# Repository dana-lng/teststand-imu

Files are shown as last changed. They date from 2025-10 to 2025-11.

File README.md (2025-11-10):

# Two-Axis IMU Calibration Test Stand with Differential Gear System
An open-source, dual-axis calibration platform for IMU sensors (e.g., MPU6050), featuring a fully 3D-printed differential gear drive and automated motion control for precise in-situ calibration.

## Project Overview

This project presents the design and function of a **two-axis IMU calibration test stand**, developed to calibrate inertial measurement units (IMUs) such as the [MPU6050](https://invensense.tdk.com/products/motion-tracking/6-axis/mpu-6050/). The test stand enables controlled, repeatable motion for precise sensor calibration.

All mechanical parts are **3D printed**, and motion is driven by **NEMA 17 stepper motors** in combination with an **HTD belt system**. The movement is realized through a **differential gear mechanism**, providing two degrees of freedom (DoF).

The Calibration is based on the method proposed in the following paper:
> **A. Mikov, S. Reginya, and A. Moschevikin**,
> *"In-situ Gyroscope Calibration Based on Accelerometer Data,"*
> 27th Saint Petersburg International Conference on Integrated Navigation Systems (ICINS), IEEE, 2020.
> [[IEEE paaper]](https://ieeexplore.ieee.org/document/9133804) and Github Repository [[imu-calib]](https://github.com/mikoff/imu-calib).

---

## Mechanical Design and Kinematics
Here you can see the Mechanical Setup in real life and in Solidworks.
<p align="left">
  
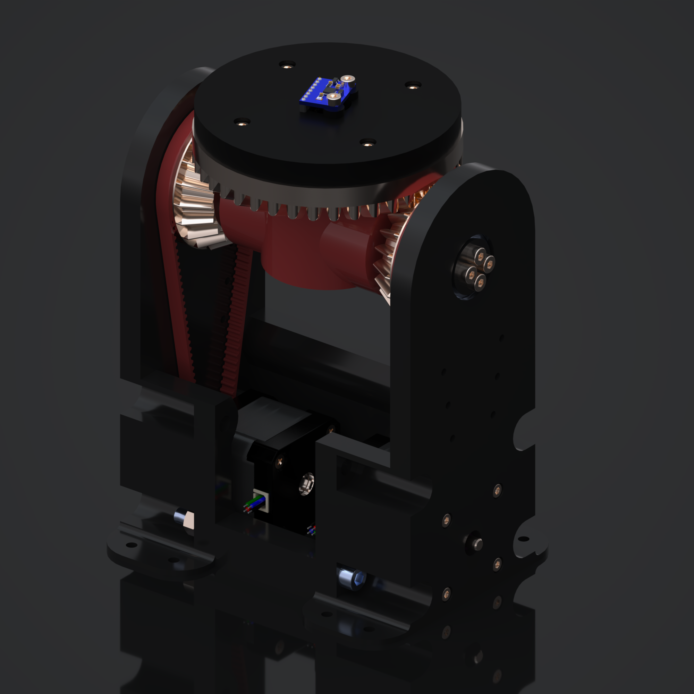
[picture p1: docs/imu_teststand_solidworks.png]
  
</p>
Below are the differential gear animations showing the independent Z-axis rotation and combined X/Z-axis motion.

<b>Z-Axis Rotation</b> &nbsp;&nbsp;&nbsp;&nbsp;&nbsp;&nbsp;&nbsp;&nbsp;&nbsp;&nbsp;&nbsp;&nbsp;&nbsp;&nbsp;&nbsp;&nbsp;&nbsp;&nbsp;&nbsp;&nbsp;&nbsp;&nbsp;&nbsp;&nbsp;&nbsp;&nbsp;&nbsp;&nbsp;&nbsp;&nbsp;&nbsp;&nbsp;&nbsp;&nbsp;&nbsp;&nbsp;&nbsp;&nbsp;&nbsp;&nbsp;&nbsp;&nbsp;&nbsp;&nbsp;&nbsp;&nbsp;&nbsp;&nbsp;&nbsp;&nbsp;&nbsp;&nbsp;&nbsp;&nbsp;&nbsp;&nbsp;&nbsp;&nbsp;&nbsp;&nbsp;&nbsp;&nbsp;&nbsp;&nbsp;&nbsp;&nbsp;&nbsp;&nbsp;&nbsp;&nbsp;&nbsp;&nbsp;&nbsp;&nbsp;&nbsp;&nbsp;&nbsp; <b>X/Y-Axis Rotation</b><br>
 

<b>Exploded Assembly View</b><br>


---

## Wiring Diagram
The wiring connects two NEMA 17 stepper drivers, an ESP32 microcontroller, and the MPU6050 IMU sensor.
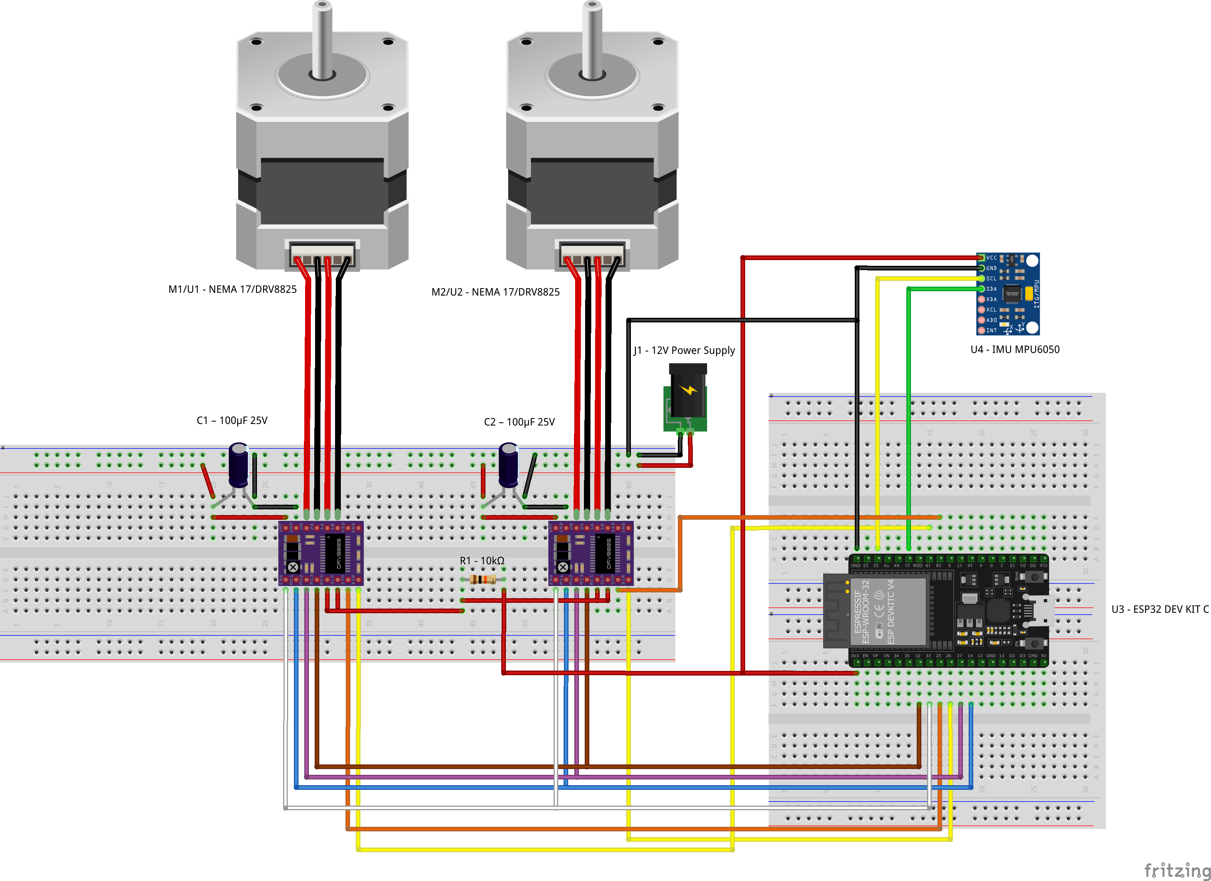
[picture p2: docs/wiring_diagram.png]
Wiring Diagram Explanation


---

## Validations
Each calibration result was obtained through a series of standstill measurements and controlled rotations performed by the test stand.
### Accelerometer Validation
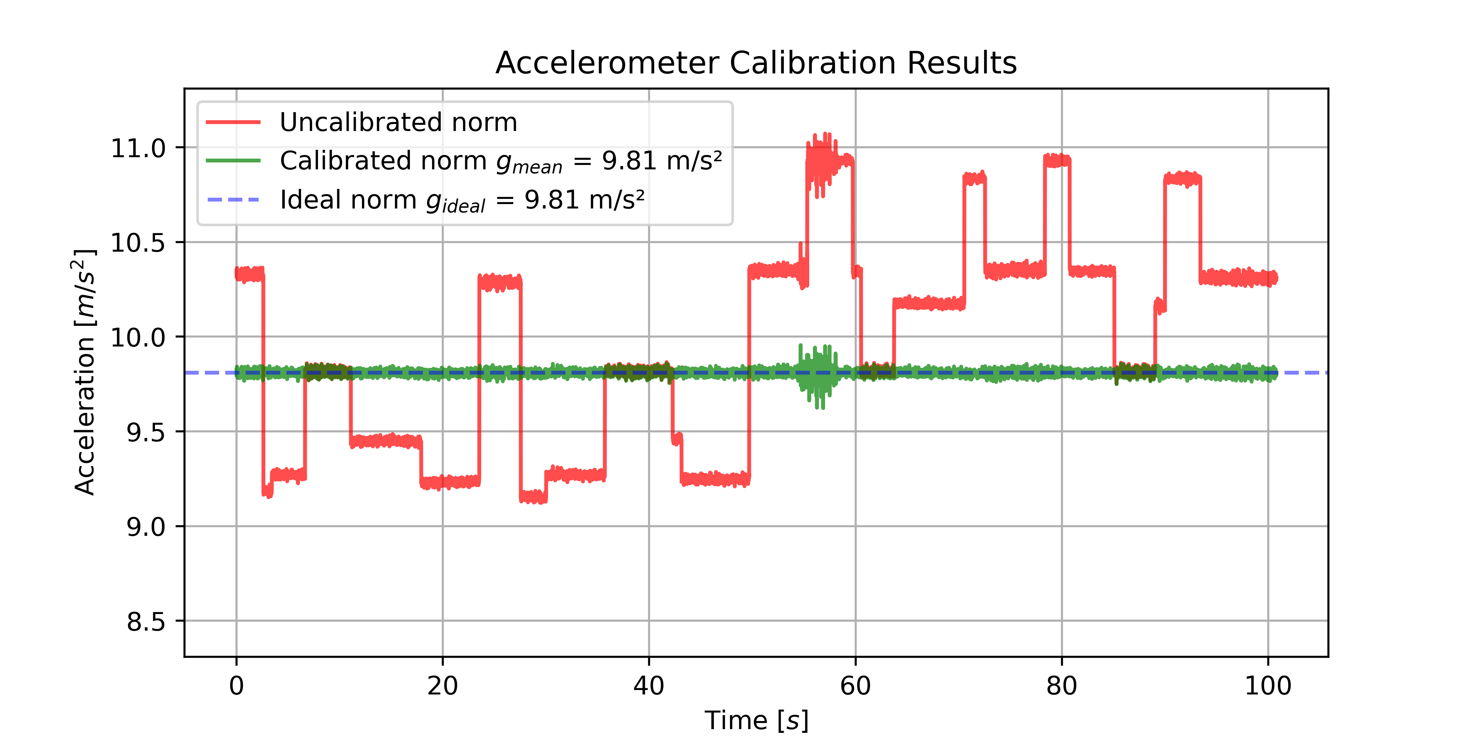
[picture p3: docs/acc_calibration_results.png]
Accelerometer Validation


### Gyroscope Validation
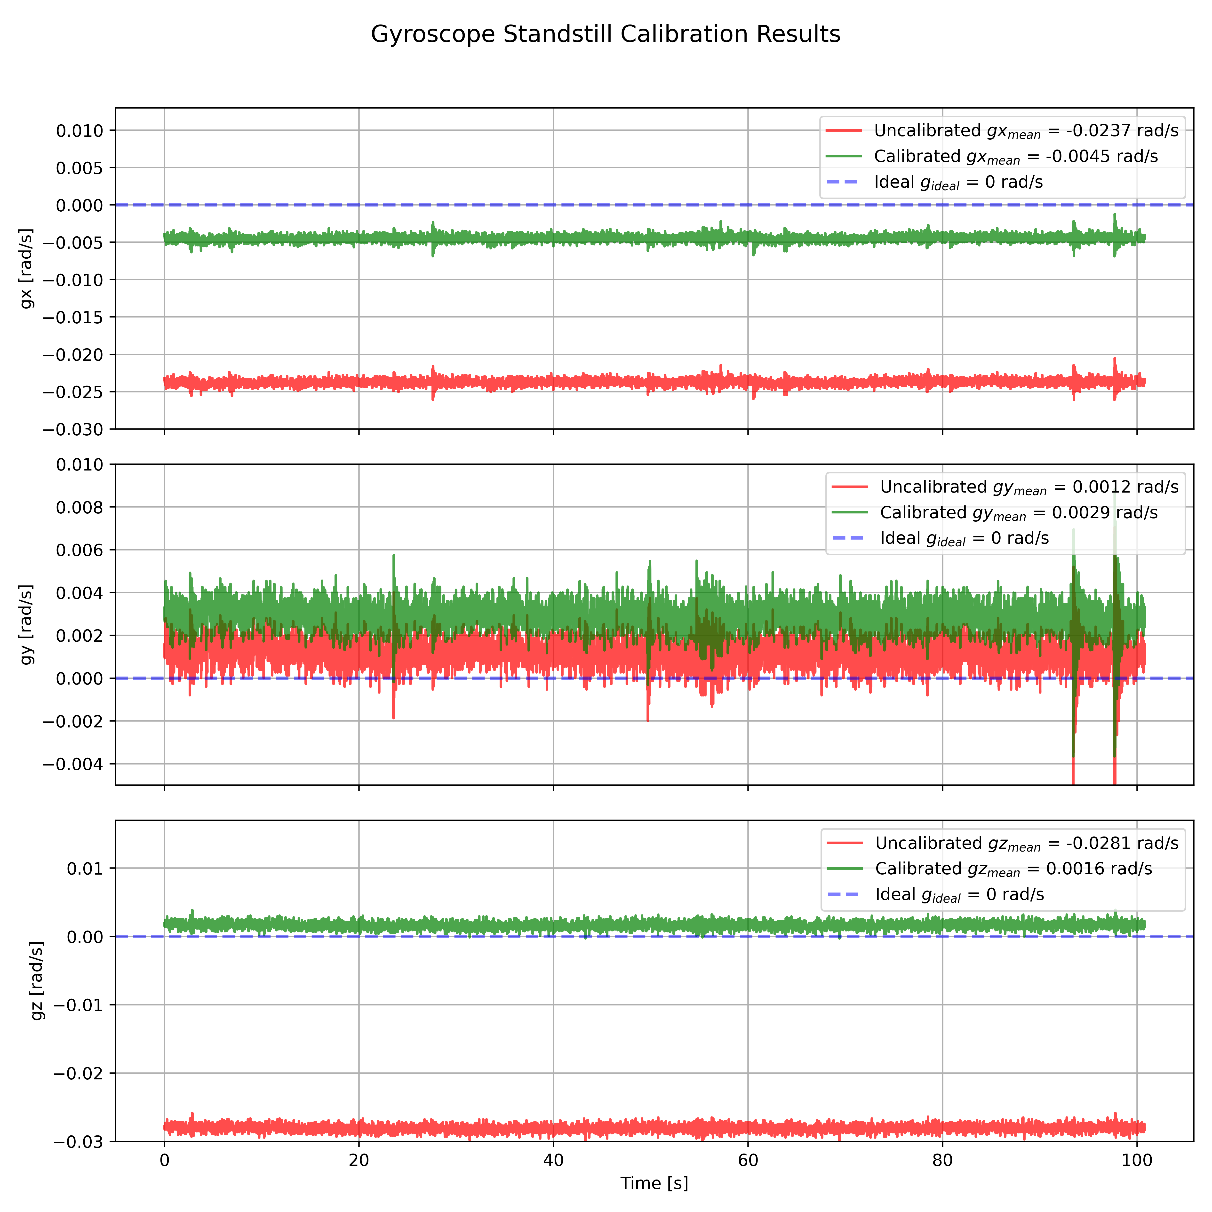
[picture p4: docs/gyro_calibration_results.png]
Gyroscope Validation


### Live Validation
Live Validation
---

## Setting Up the Test Stand
Eventually you have to set the correct COM port in the [main GUI](software/python/src/gui/main.py) before running it.
### Prerequisites
```bash
# Clone the repository
git clone https://github.com/anh-lxn/teststand-imu.git
cd teststand-imu

# Create and activate a virtual environment
python -m venv software/python/venv
source software/python/venv/bin/activate   # (Linux/macOS)
# .\software\python\venv\Scripts\activate  # (Windows)

# Install required dependencies
pip install -r software/python/requirements.txt
```

### Compiling and Uploading Firmware to ESP32
The software C++ File for the ESP32 is located under: [cpp folder](software/cpp/)
To build and upload the firmware, you need PlatformIO installed in your IDE (e.g., VSCode).

```bash
# Build and upload the firmware to the ESP32
pio run --target upload

# (Optional) Open the serial monitor
pio device monitor
```

Please note that it takes a few seconds for the ESP32 to boot up after uploading the firmware. (For me its around 30 seconds)

### Running the Graphical Interface
```bash
# Run the main GUI application
python software/python/src/gui/main.py
```
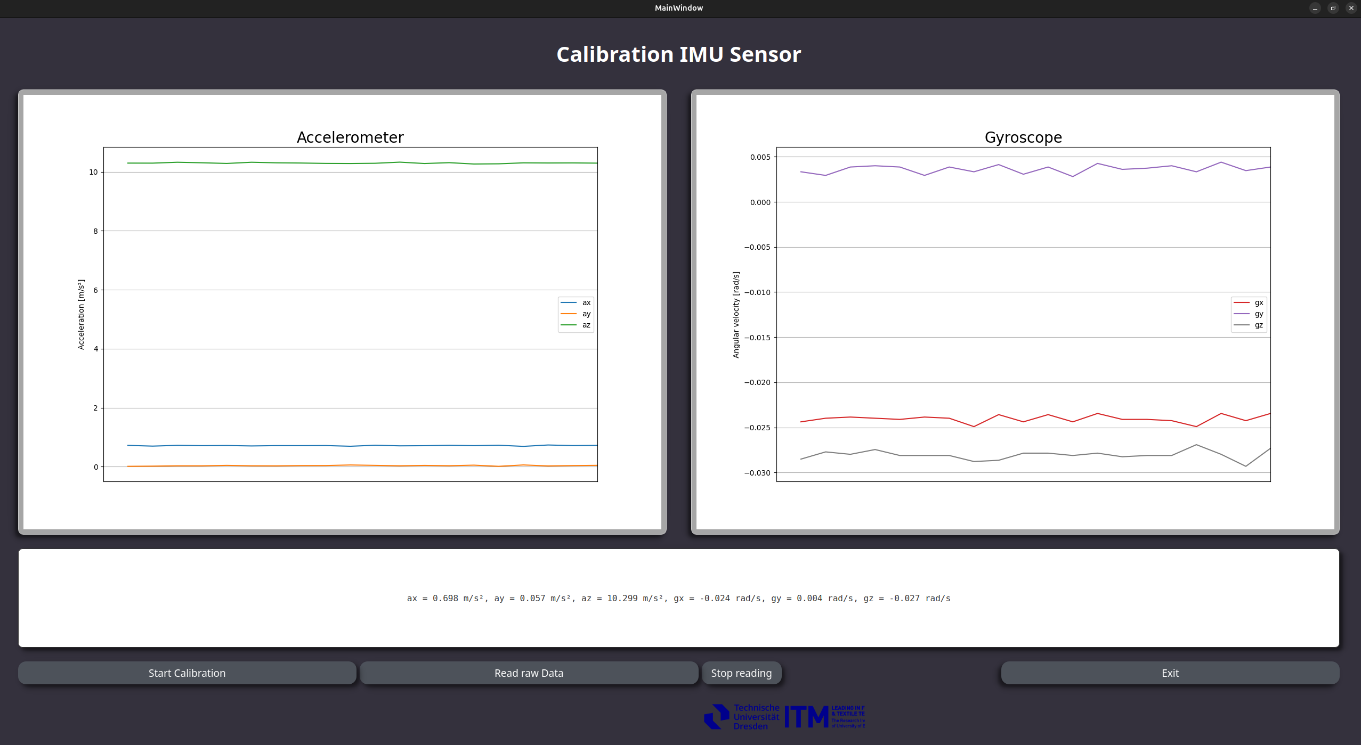
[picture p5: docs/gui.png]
MAIN GUI


Buttons:
- **Start Calibration**: The Imu will collect Data in synchronization with the Test Stand Movement. Then it will perform the Calibration and show the Results and save them in the results folder.
- **Read raw data**: The Imu will send raw data to the GUI for live visualization without performing calibration.
- **Stop reading**: Stops any ongoing data reading from the Imu.

### Running Validation Scripts
```bash
# Run accelerometer validation
python software/python/src/accel_validation.py
```

```bash
# Run gyroscope standstill validation
python software/python/src/gyro_standstill_validation.py
```
```bash
# Run live validation
python software/python/src/live_validation.py
```
---

## Authors and Contributors

- **[Anh Le Xuan](https://www.anhlexuan.com)** – Student Assistant
  Designed, built, and programmed the complete IMU test stand, including 3D modeling, electronics, firmware, and software.

- **[Dana Lenzig](https://www.linkedin.com/in/dana-lenzig-61a04830a)** – Student Assistant
  Developed the graphical user interface (GUI) for live visualization and calibration control.

- **Benjamin Waschilewski** – Research Associate and Project Supervisor
- **Hung Le Xuan** – Head of Research Group

*Institute of Textile Machinery and High Performance Material Technology (ITM), TU Dresden*

### Citation

If you use this project or parts of it, please give credit to the following authors:

> **Anh Le Xuan**, **Dana Lenzig**, **Benjamin Waschilewski**, **Hung Le Xuan**
> *Institute of Textile Machinery and High Performance Material Technology (ITM), TU Dresden*
>
> Based on the calibration method described in:
> *Mikov, A., Reginya, S., & Moschevikin, A. (2020). In-situ Gyroscope Calibration Based on Accelerometer Data.
> 2020 27th Saint Petersburg International Conference on Integrated Navigation Systems (ICINS), IEEE.*

---

## License
This project is released under the MIT License.
See [LICENSE](./LICENSE) for details.

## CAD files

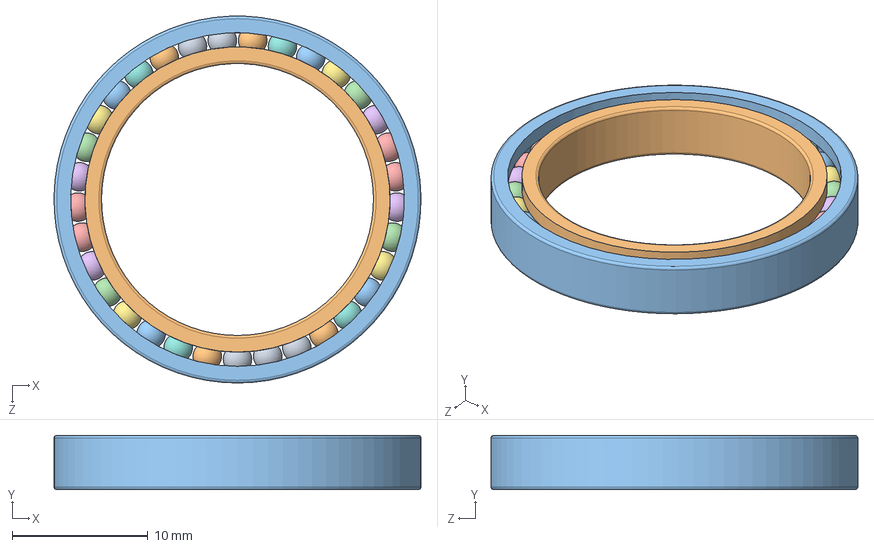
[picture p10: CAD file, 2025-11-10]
cad/Pack and Go/Radialrillenkugellager 6704 20x27x4.SLDASM
27.0 x 4.00 x 27.0 mm

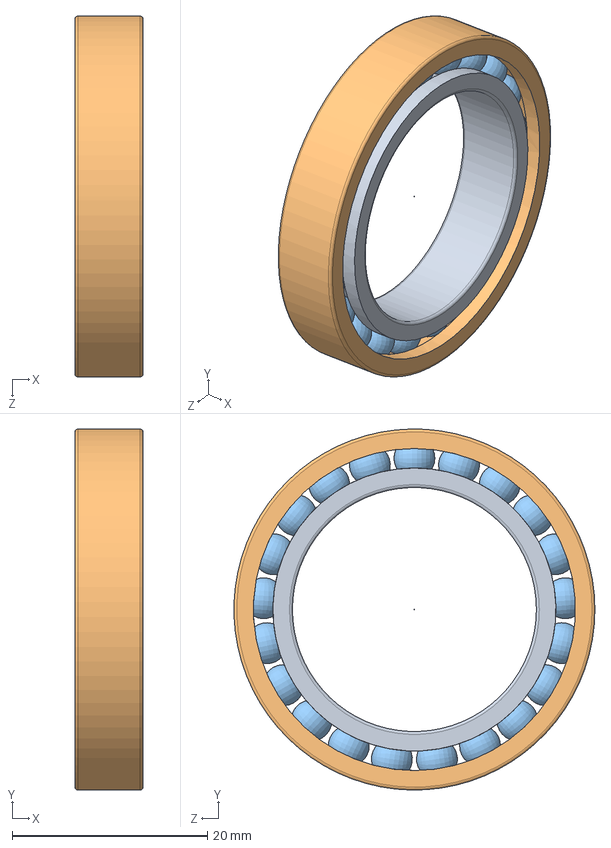
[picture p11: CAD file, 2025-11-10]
cad/Kegelrad/Radialrillenkugellager 6805 25x37x7/Radialrillenkugellager 6805 25x37x7.SLDASM
7.00 x 37.0 x 37.0 mm
bearing_6805_01
bearing_6805_02
bearing_6805_03

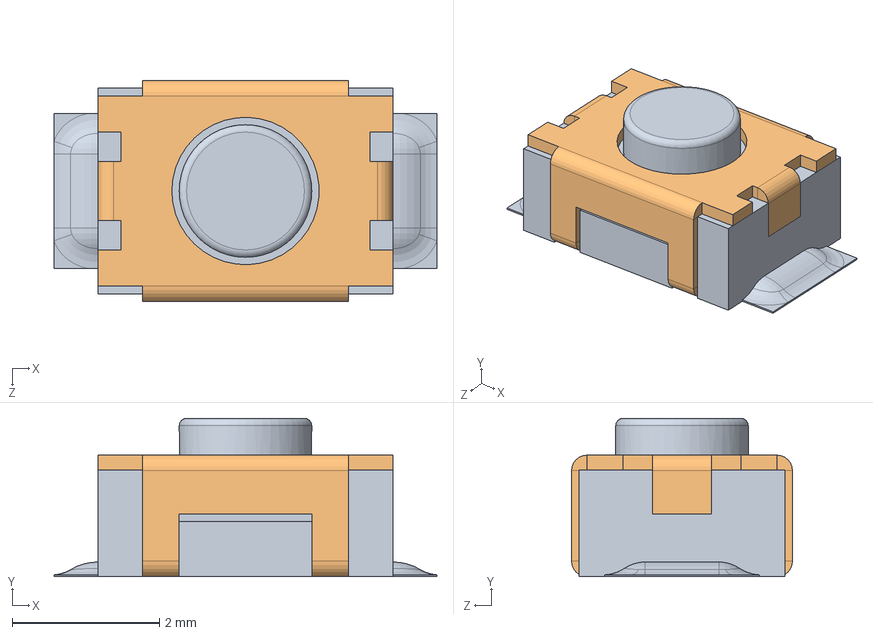
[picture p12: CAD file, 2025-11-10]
cad/Elektronik/arduino nano/reset button.SLDASM
5.20 x 2.15 x 3.00 mm
reset core
reset shell

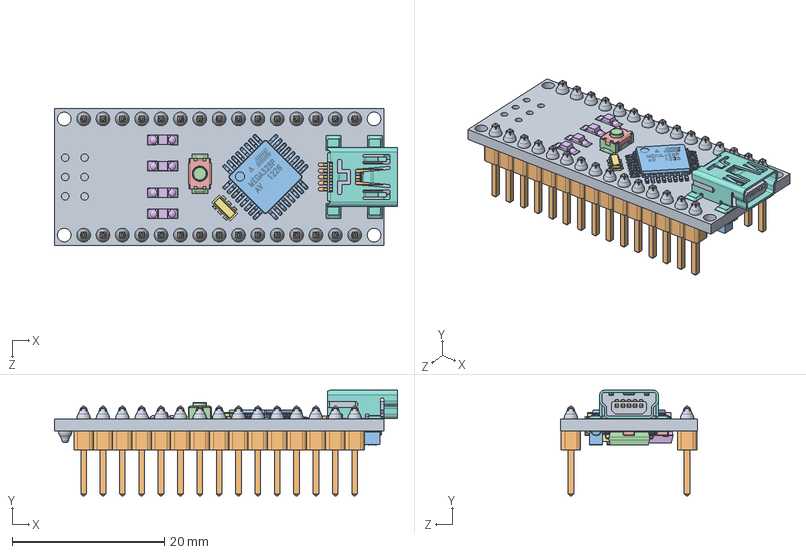
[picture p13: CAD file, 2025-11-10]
cad/Elektronik/arduino nano/arduino nano.SLDASM
45.0 x 13.9 x 18.0 mm
nano-board
15pin_header__ x 2
atmega328
ftdi FT232rl
smt_resistor222 x 5
led x 4
16mhz crystal - measured
MINIUSBSHELL
MINIUSBCORE
MINI USB CONTACT x 5
cap106C x 2
reset core
reset shell
nano - reg
NANO DIODE
189 RESISTOR PACK
102 RESISTOR PACK

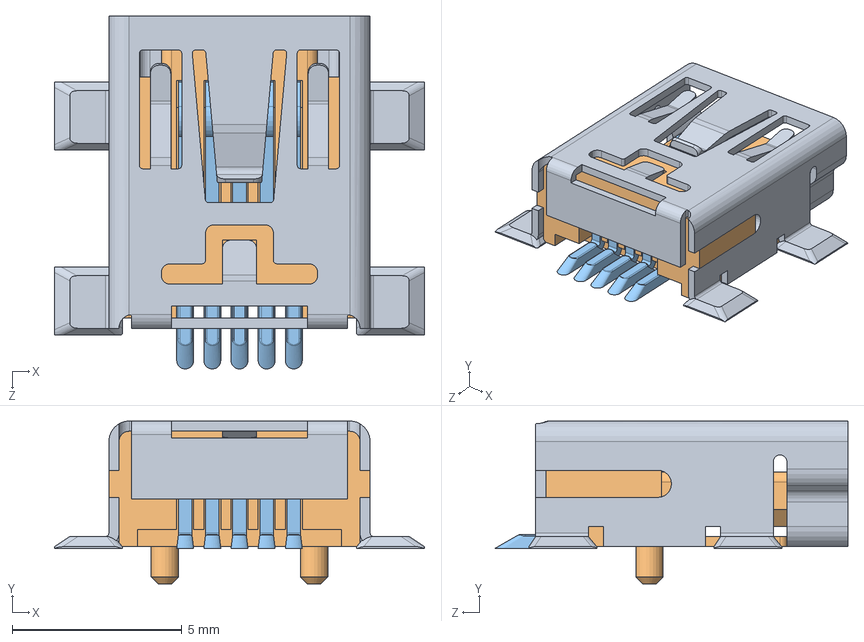
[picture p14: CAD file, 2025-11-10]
cad/Elektronik/arduino nano/MINIUSB - MEASURED.SLDASM
10.9 x 4.80 x 10.4 mm
MINIUSBSHELL
MINIUSBCORE
MINI USB CONTACT x 5

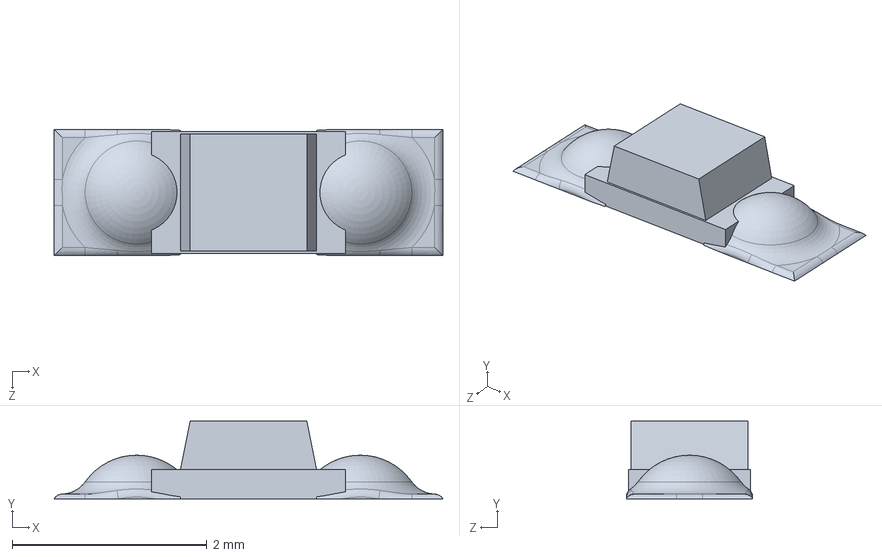
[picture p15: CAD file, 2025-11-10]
cad/Elektronik/arduino nano/led.SLDPRT
4.00 x 0.8 x 1.30 mm

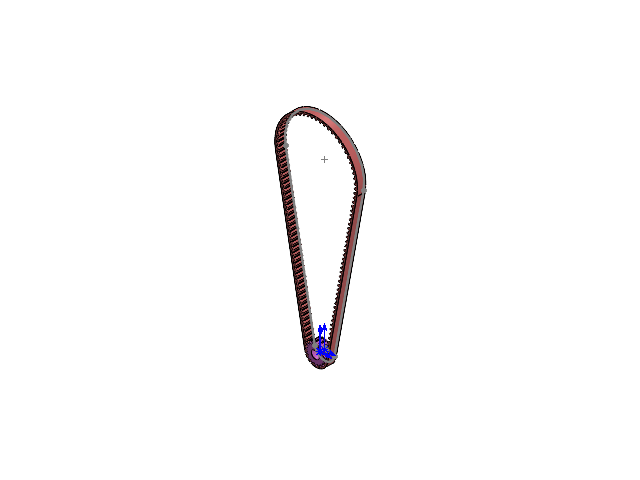
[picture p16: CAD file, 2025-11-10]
cad/Motorantrieb/Motorantrieb.SLDASM
Motorantrieb_Zahnriemen
Riemen3-4

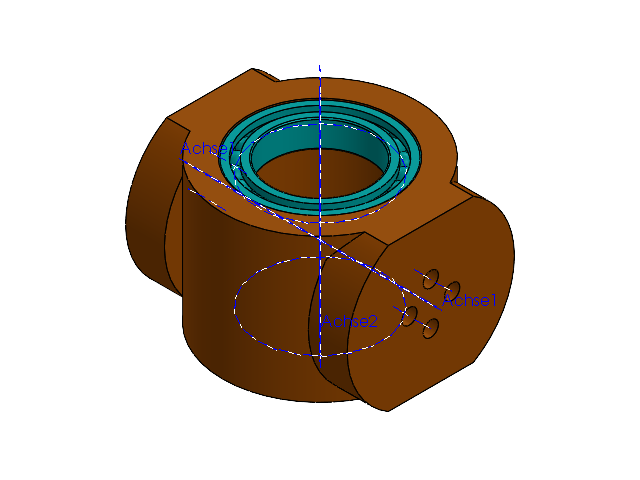
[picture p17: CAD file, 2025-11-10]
cad/Kegelrad/Getriebehub_Baugruppe.SLDASM
Getriebehub
bearing_6805_01 x 2
bearing_6805_02 x 2
bearing_6805_03 x 2

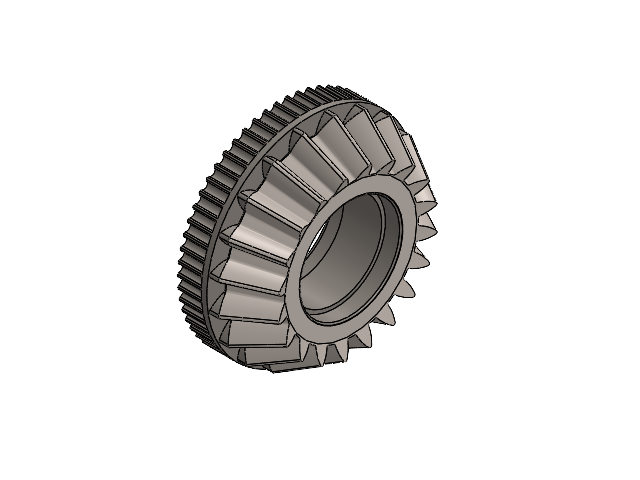
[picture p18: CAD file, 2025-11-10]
cad/Ritzel/Ritzel.SLDASM
Zahnraderweiterung
Ritzel_Custom

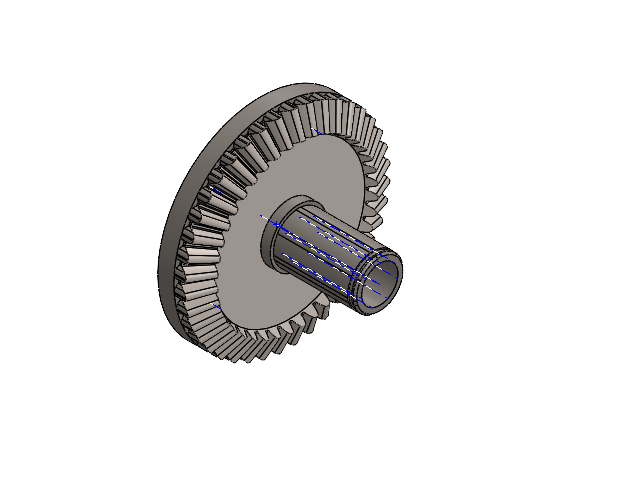
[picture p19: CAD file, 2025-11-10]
cad/Kegelrad/Kegelrad.SLDASM
Kegelrad_Custom
Zahnraderweiterung Kegelrad

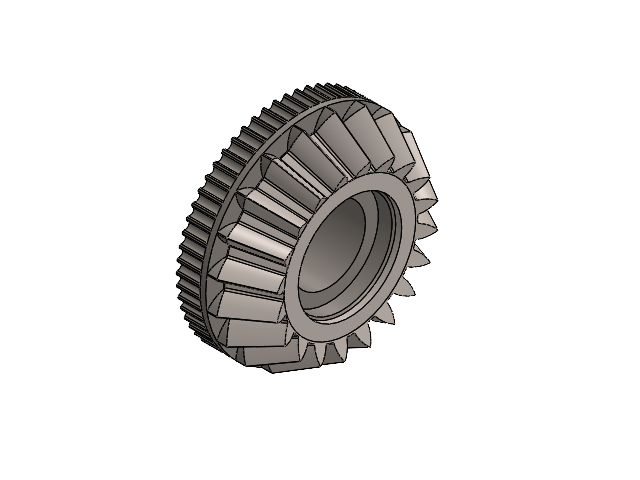
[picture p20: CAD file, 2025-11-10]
cad/Pack and Go/Ritzel.SLDASM
Zahnraderweiterung
straight bevel pinion_iso

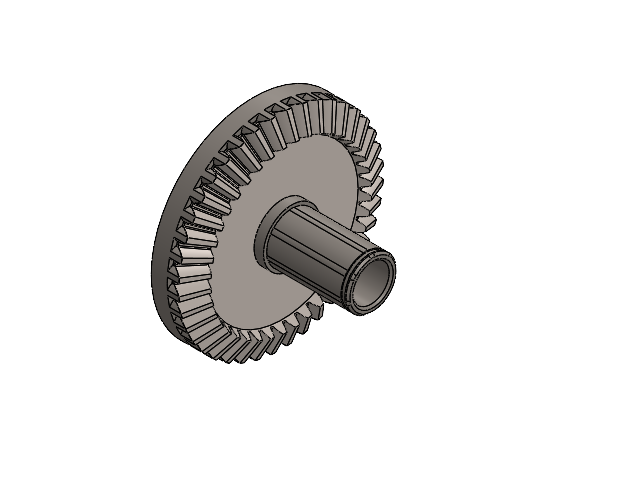
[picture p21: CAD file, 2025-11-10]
cad/Pack and Go/Kegelrad.SLDASM
straight bevel gear_iso
Zahnraderweiterung Kegelrad

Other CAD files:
cad/Radialrillenkugellager 6704 20x27x4/Radialrillenkugellager 6704 20x27x4.SLDASM
cad/Pack and Go/reset button.SLDASM
cad/Pack and Go/Radialrillenkugellager 6805 25x37x7.SLDASM
cad/Pack and Go/arduino nano.SLDASM
cad/Pack and Go/MINIUSB - MEASURED.SLDASM
cad/Pack and Go/Getriebehub_Baugruppe.SLDASM
cad/#archiv/12_teeth_pulley1.SLDPRT
cad/#archiv/1_mm_spacer.SLDPRT
cad/#archiv/Magnet_shaft.SLDPRT
cad/#archiv/Motor_holder_2.SLDPRT
cad/#archiv/Rad.SLDPRT
cad/#archiv/Schrägzahnrad für Zahnriemen.SLDPRT
cad/#archiv/big_bevel.SLDPRT
cad/#archiv/big_bevel_backplate.SLDPRT
cad/#archiv/gear_hub_single_stage.SLDPRT
cad/#archiv/outer_shell_part.SLDPRT
cad/#archiv/ritzel/01_Ritzel-Kegel.dxf
cad/#archiv/small_bevel.SLDPRT
cad/#archiv/small_bevel_backplate.SLDPRT
cad/#archiv/small_bevel_shaft.SLDPRT
cad/Elektronik/MPU6050 Module.step
cad/Elektronik/arduino nano/102 RESISTOR PACK.SLDPRT
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

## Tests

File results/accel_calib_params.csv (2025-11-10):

S_X | S_Y | S_Z | NO_X | NO_Y | NO_Z | B_X | B_Y | B_Z
0.0043 | 0.0037 | 0.0212 | 0.0016 | -0.0 | 0.0067 | 1.0822 | -0.0753 | 0.2884

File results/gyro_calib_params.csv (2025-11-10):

S_X | S_Y | S_Z | NO_X | NO_Y | NO_Z | B_X | B_Y | B_Z | E_X | E_Y | E_Z
-0.0012 | -0.0099 | -0.0041 | 0.0142 | 0.002 | -0.047 | -0.0187 | -0.0017 | -0.0301 | 0.0009 | 0.0175 | 0.0018

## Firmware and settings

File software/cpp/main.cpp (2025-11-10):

#include <Arduino.h>
#include <AccelStepper.h>
#include <Wire.h>

// ===== Threads =====
TaskHandle_t TaskMotorHandle;   // Task-Handle-Variable
TaskHandle_t TaskIMUHandle;
// ===== Zustände & Variablen =====
bool motor_enabled = false;
volatile bool motor_done = false;
volatile bool read_imu = false;
volatile bool start_calib = false;
int transitionSpeed = 10000;
float dt = 8; // Default: 2s
int stillstands = 6; // Default: 10 // Eventuell Ändern auf 8 oder 6
float degreeZ = 180; // Default: 45.0
int rotation_count = 0;
float beschleunigung = 10000.0;

// ===== Pins =====
#define DIR_PIN_1 26
#define DIR_PIN_2 19
#define STEP_PIN_1 18
#define STEP_PIN_2 25
#define ENABLE_PIN 33
#define M0_PIN 14
#define M1_PIN 27
#define M2_PIN 32

// ===== Kinematik =====
const float zaehne_Zahnriemen = 15.0f;
const float zaehne_Ritzel = 59.0f;
const float uebersetzung = (zaehne_Ritzel / zaehne_Zahnriemen) / 2.0;
const float vollSchritteproUmdrehung = 200;
int microstepping = 16;
float mikroSchritteProUmdrehung = vollSchritteproUmdrehung * microstepping;

AccelStepper stepper1(AccelStepper::DRIVER, STEP_PIN_1, DIR_PIN_1);
AccelStepper stepper2(AccelStepper::DRIVER, STEP_PIN_2, DIR_PIN_2);
const unsigned long startDelayMs = 3000;
unsigned long t0;

// ===== Funktionen =====
float berechneMikroschritteProSekunde(float winkelgeschwindigkeit) {
  float winkelgeschwindigkeit_motor = winkelgeschwindigkeit * uebersetzung;
  float umdrehungen_pro_sekunde = winkelgeschwindigkeit_motor / 360;
  return umdrehungen_pro_sekunde * mikroSchritteProUmdrehung;
}

float berechneMikroschritteProDrehung(float rotation) {
  return rotation * mikroSchritteProUmdrehung * uebersetzung;
}

// ===== Setup Motorpins =====
void starte_kinematik_setup() {
  pinMode(STEP_PIN_1, OUTPUT);
  pinMode(STEP_PIN_2, OUTPUT);
  pinMode(DIR_PIN_1, OUTPUT);
  pinMode(DIR_PIN_2, OUTPUT);
  pinMode(M0_PIN, OUTPUT);
  pinMode(M1_PIN, OUTPUT);
  pinMode(M2_PIN, OUTPUT);
  pinMode(ENABLE_PIN, OUTPUT);
  digitalWrite(ENABLE_PIN, HIGH); // deaktiviert
  digitalWrite(M0_PIN, HIGH);
  digitalWrite(M1_PIN, HIGH);
  digitalWrite(M2_PIN, LOW);

  stepper1.setMinPulseWidth(5);
  stepper1.setAcceleration(beschleunigung);
  stepper1.setCurrentPosition(0);
  stepper2.setMinPulseWidth(5);
  stepper2.setAcceleration(beschleunigung/2);
  stepper2.setCurrentPosition(0);
}


void disableMotor() {
  digitalWrite(ENABLE_PIN, HIGH);
  motor_enabled = false;
}

void enableMotor() {
  digitalWrite(ENABLE_PIN, LOW);
  motor_enabled = true;;
}

// ===== Gleichverteilte Zufallslisten =====
void init_random_profiles(float *zufall_dt_values, float *zufall_values, int n) {
  float dt_min = 2.0, dt_max = 8.0;
  float val_min = 10.0, val_max = 40.0;

  // gleichmäßig verteilen
  for (int i = 0; i < n; i++) {
    zufall_dt_values[i] = dt_min + i * (dt_max - dt_min) / (n - 1);
    zufall_values[i] = val_min + i * (val_max - val_min) / (n - 1);
  }

  // Fisher-Yates Shuffle
  for (int i = n - 1; i > 0; i--) {
    int j = random(0, i + 1);
    float tmp = zufall_dt_values[i];
    zufall_dt_values[i] = zufall_dt_values[j];
    zufall_dt_values[j] = tmp;

    tmp = zufall_values[i];
    zufall_values[i] = zufall_values[j];
    zufall_values[j] = tmp;
  }
}

// ===== Bewegung in Stillstandspositionen =====
void fahre_stillstandspositionen_ab(int motor) {
  //float rotation = 2.0 / stillstands;
  float deg = 360.0 / stillstands;
  float rotation = deg * 2 / 360.0;

  // Zufallslisten erzeugen
  float zufall_dt_values[stillstands];
  float zufall_values[stillstands];
  init_random_profiles(zufall_dt_values, zufall_values, stillstands);

  if (motor == 1) {

    for (int i = 0; i < stillstands; i++) {
      disableMotor();
      float zufall_dt = zufall_dt_values[i];  // reproduzierbar & verteilt
      vTaskDelay(zufall_dt * 1000 / portTICK_PERIOD_MS); // Stillstandzeit
      enableMotor();
      digitalWrite(DIR_PIN_1, LOW);

      float zufall = zufall_values[i];        // reproduzierbar & verteilt
      float winkelgeschwindigkeit = deg * zufall / dt;
      stepper1.setMaxSpeed(berechneMikroschritteProSekunde(winkelgeschwindigkeit));

      float mikroSchritteInsgesamt = berechneMikroschritteProDrehung(rotation);
      long ziel = stepper1.currentPosition() + mikroSchritteInsgesamt;
      Serial.print("Motor1 Schritte: "); Serial.println(ziel);
      stepper1.moveTo(ziel);
      // Bewegung laufen lassen, ohne zu blockieren
      while (stepper1.distanceToGo() != 0) { stepper1.run(); }
      stepper1.setCurrentPosition(0);
    }
  }
  else if (motor == 2){

    for (int i = 0; i < stillstands; i++) {
      disableMotor();
      float zufall_dt = zufall_dt_values[i];  // reproduzierbar & verteilt; // Ändern auf 8 und 2?
      vTaskDelay(zufall_dt * 1000 / portTICK_PERIOD_MS); // Stillstandzeit
      enableMotor();
      digitalWrite(DIR_PIN_2, LOW);
      float zufall = zufall_values[i];        // reproduzierbar & verteilt
      float winkelgeschwindigkeit = deg * zufall / dt;
      stepper2.setMaxSpeed(berechneMikroschritteProSekunde(winkelgeschwindigkeit)/2);

      float mikroSchritteInsgesamt = berechneMikroschritteProDrehung(rotation);
      long ziel = stepper2.currentPosition() + mikroSchritteInsgesamt /2;
      Serial.print("Motor2 Schritte: "); Serial.println(ziel);
      stepper2.moveTo(ziel);
      // Bewegung laufen lassen, ohne zu blockieren
      while (stepper2.distanceToGo() != 0) { stepper2.run(); }
      stepper2.setCurrentPosition(0);
    }
  }


}

void homing() {
  float rotation = 2.0;  // wie vorher
  float richtungsfaktor = -1.0; // immer rückwärts

  stepper1.setAcceleration(5000);
  stepper2.setAcceleration(5000/2);
  // Geschwindigkeit setzen
  stepper1.setMaxSpeed(transitionSpeed);
  stepper2.setMaxSpeed(transitionSpeed / 2);

  // Zielpositionen (negativ für Rückwärtsdrehung)
  long ziel1 = stepper1.currentPosition() + richtungsfaktor * berechneMikroschritteProDrehung(rotation);
  long ziel2 = stepper2.currentPosition() + richtungsfaktor * berechneMikroschritteProDrehung(rotation) / 2;

  stepper1.moveTo(ziel1);
  stepper2.moveTo(ziel2);

  // Bewegung ausführen
  while (stepper1.distanceToGo() != 0 || stepper2.distanceToGo() != 0) {
    stepper1.run();
    stepper2.run();
  }

  // Position zurücksetzen (optional)
  stepper1.setCurrentPosition(0);
  stepper2.setCurrentPosition(0);
  stepper1.setAcceleration(beschleunigung);
  stepper2.setAcceleration(beschleunigung/2);
}

void transitionZ() {
  stepper1.setAcceleration(5000);
  stepper2.setAcceleration(5000/2);
  // Geschwindigkeit für Übergangsbewegung setzen
  stepper1.setMaxSpeed(transitionSpeed);
  stepper2.setMaxSpeed(transitionSpeed/2);

  // Rotation berechnen: degreeZ (z. B. 60 °)
  float rotation = (degreeZ / 360.0) * 2.0;   // *2 wegen Übersetzung
  float richtungsfaktor = -1.0; // immer rückwärts

  // Zielposition berechnen und Bewegung starten
  long ziel1 = stepper1.currentPosition() + berechneMikroschritteProDrehung(rotation);
  long ziel2 = stepper2.currentPosition() + berechneMikroschritteProDrehung(rotation) / 2;
  stepper1.moveTo(ziel1);
  stepper2.moveTo(ziel2);

  // Bewegung ausführen, nicht blockierend
  while (stepper1.distanceToGo() != 0 || stepper2.distanceToGo() != 0) {
    stepper1.run();
    stepper2.run();
  }
  stepper1.setAcceleration(beschleunigung);
  stepper2.setAcceleration(beschleunigung/2);
}

void transition_cable() {
  stepper1.setAcceleration(5000);
  stepper2.setAcceleration(5000/2);
  float rotation = 2.0;  // wie vorher
  float richtungsfaktor = -1.0; // immer rückwärts

  // Geschwindigkeit setzen
  stepper1.setMaxSpeed(transitionSpeed);
  stepper2.setMaxSpeed(transitionSpeed / 2);

  // Zielpositionen (negativ für Rückwärtsdrehung)
  long ziel1 = stepper1.currentPosition() + richtungsfaktor * berechneMikroschritteProDrehung(rotation);
  long ziel2 = stepper2.currentPosition() + richtungsfaktor * berechneMikroschritteProDrehung(rotation) / 2;

  stepper1.moveTo(ziel1);
  stepper2.moveTo(ziel2);

  // Bewegung ausführen
  while (stepper1.distanceToGo() != 0 || stepper2.distanceToGo() != 0) {
    stepper1.run();
    stepper2.run();
  }

  // Position zurücksetzen (optional)
  stepper1.setCurrentPosition(0);
  stepper2.setCurrentPosition(0);
  stepper1.setAcceleration(beschleunigung);
  stepper2.setAcceleration(beschleunigung/2);

}

// ===== MPU =====
const uint8_t MPU = 0x68;
const float g0 = 9.81;
const float MPUscaleFactorAcc = 16384.0;
const float MPUscaleFactorAccMS2 = g0 / MPUscaleFactorAcc;
const float MPUscaleFactorGyro = 131.0;
const float MPUscaleFactorGyroRADS = MPUscaleFactorGyro / (PI / 180.0);

void writeReg(uint8_t reg, uint8_t val) {
  Wire.beginTransmission(MPU);
  Wire.write(reg);
  Wire.write(val);
  Wire.endTransmission(true);
}

void mpu_setup(uint16_t rate_hz = 100) {
  writeReg(0x6B, 0x01);
  writeReg(0x6C, 0x00);
  writeReg(0x1B, 0x00);
  writeReg(0x1C, 0x00);
  writeReg(0x1A, 0x04);
  uint8_t div = (uint8_t)(1000 / rate_hz - 1);
  writeReg(0x19, div);
  writeReg(0x6A, 0x04);
}

void readDataIMU() {
  Wire.beginTransmission(MPU);
  Wire.write(0x3B);
  Wire.endTransmission(false);
  Wire.requestFrom(MPU, 14, true);
  if (Wire.available() == 14) {
    int16_t ax = (Wire.read() << 8) | Wire.read();
    int16_t ay = (Wire.read() << 8) | Wire.read();
    int16_t az = (Wire.read() << 8) | Wire.read();
    Wire.read(); Wire.read();
    int16_t wx = (Wire.read() << 8) | Wire.read();
    int16_t wy = (Wire.read() << 8) | Wire.read();
    int16_t wz = (Wire.read() << 8) | Wire.read();
    Serial.print((float)ax * MPUscaleFactorAccMS2, 5); Serial.print(",");
    Serial.print((float)ay * MPUscaleFactorAccMS2, 5); Serial.print(",");
    Serial.print((float)az * MPUscaleFactorAccMS2, 5); Serial.print(",");
    Serial.print((float)wx / MPUscaleFactorGyroRADS, 5); Serial.print(",");
    Serial.print((float)wy / MPUscaleFactorGyroRADS, 5); Serial.print(",");
    Serial.println((float)wz / MPUscaleFactorGyroRADS, 5);
  }
}


// ===== Task: Pyserial =====
void TaskPySerial(void *pvParameters) {
  for (;;) {
    if (Serial.available()) {
      String cmd = Serial.readStringUntil('\n');
      // Signale
      if (cmd == "Start Raw Read") { Serial.println("Signal received."); read_imu = true; }
      else if (cmd == "Stop Raw Read") { Serial.println("Signal received."); read_imu = false; }
      else if (cmd == "Start Calibration") { Serial.println("Signal received."); start_calib = true; }
      else if (cmd == "Test") { Serial.println("Signal received."); start_calib = false; }
    }
    vTaskDelay(10 / portTICK_PERIOD_MS);
  }
}

// ===== Task: IMU =====
void TaskReadIMU(void *pvParameters) {
  const TickType_t period = pdMS_TO_TICKS(10); // 100 Hz
  TickType_t lastWake = xTaskGetTickCount();

  for (;;) {
    if (read_imu) {
      readDataIMU();
      vTaskDelayUntil(&lastWake, period); // <-- absoluter Takt, konstante Rate
    } else {
      vTaskDelay(pdMS_TO_TICKS(50));
      lastWake = xTaskGetTickCount();     // Takt resetten wenn pausiert
    }
  }
}

/*
void TaskMotor(void *pvParameters) {
  for (;;) {
    if (start_calib) {
      fahre_stillstandspositionen_ab(1);
      vTaskDelay(100 / portTICK_PERIOD_MS);
    }

  }
}
*/


void TaskMotor(void *pvParameters) {
  for (;;) {
    if (start_calib) {
      read_imu = true;
      if (rotation_count % 2 == 0) {
        //Serial.print("rotation: "); Serial.println(rotation_count);
        fahre_stillstandspositionen_ab(1);
        vTaskDelay(10 / portTICK_PERIOD_MS);
        rotation_count++;
      }
      else {
        //Serial.print("rotation: "); Serial.println(rotation_count);
        fahre_stillstandspositionen_ab(2);
        read_imu = false;
        vTaskDelay(10 / portTICK_PERIOD_MS);
        transition_cable();
        vTaskDelay(100 / portTICK_PERIOD_MS);
        transitionZ();
        rotation_count++;
      }
      //randomSeed(42 + rotation_count);

      if (rotation_count >= (int)(360.0 * 2/ degreeZ)) {
        read_imu = true;
        vTaskDelay(dt * 1000 / portTICK_PERIOD_MS);
        read_imu = false;
        motor_done = true;
        start_calib = false;
        rotation_count = 0;
        homing();
        disableMotor();
        Serial.println("Calibration Done.");
        vTaskDelay(1000 / portTICK_PERIOD_MS);
      }

      vTaskDelay(1 / portTICK_PERIOD_MS);

    }
    else {
      vTaskDelay(50 / portTICK_PERIOD_MS);
    }
  }
}



// ===== Setup =====
void setup() {
  delay(10000);
  Serial.begin(115200);
  randomSeed(40);
  starte_kinematik_setup();
  Wire.begin(21, 22);
  Wire.setClock(400000);
  mpu_setup();
  delay(100);
  Serial.println("ESP32 Dual-Core Motor+IMU gestartet.");

  xTaskCreatePinnedToCore(TaskReadIMU, "TaskIMU", 8192, NULL, 2, &TaskIMUHandle, 0);
  xTaskCreatePinnedToCore(TaskMotor, "TaskMotor", 8192, NULL, 2, &TaskMotorHandle, 1);
  xTaskCreatePinnedToCore(TaskPySerial, "TaskSerial", 4096, NULL, 1, NULL, 0);

}

void loop() {}

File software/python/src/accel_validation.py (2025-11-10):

"""Accelerometer validation """

import os
import numpy as np
import pandas as pd
import matplotlib.pyplot as plt


# === PATH CONFIGURATION ===
BASE_DIR = os.path.dirname(os.path.abspath(__file__))
DATA_DIR = os.path.join(BASE_DIR, "../../..", "data")
DOCS_DIR = os.path.join(BASE_DIR, "../../..", "docs")
RESULTS_DIR = os.path.join(BASE_DIR, "../../..", "results")
CSV = os.path.join(DATA_DIR, "data.csv")
ACCEL_CALIB = os.path.join(RESULTS_DIR, "accel_calib_params.csv")
FIG = os.path.join(DOCS_DIR, "acc_calibration_results.png")


# === LOAD DATA ===
imu_data = pd.read_csv(CSV).to_numpy()
accs = imu_data[:, 0:3]


# === ACCELEROMETER CALIBRATION PARAMETERS===
acc_params = pd.read_csv(ACCEL_CALIB).to_numpy().flatten()

# === SENSOR MODEL ===
def sensor_error_model(errors):
    """
    Construct the sensor error model matrix (M) and bias vector (b)
    according to eq. (1) and (2) from the calibration model.
    """
    KX, KY, KZ, NOX, NOY, NOZ, BX, BY, BZ = errors
    M = np.array([
        [1.0 + KX, NOY, NOZ],
        [0.0, 1.0 + KY, NOX],
        [0.0, 0.0, 1.0 + KZ]
    ])
    b = np.array([BX, BY, BZ])
    return M, b


# === ACCELEROMETER CALIBRATION ===
def calibrate_accelerometer(measurements, sensor_errors):
    """
    Apply calibration to accelerometer measurements.
    See eq. (7) in the referenced calibration paper.
    """
    M, b = sensor_error_model(sensor_errors)
    C = np.linalg.inv(M)

    calibrated = np.copy(measurements)
    for m in calibrated:
        m[:] = C @ (m - b)
    return calibrated


# === STANDSTILL DETECTION ===
def generate_standstill_flags(imu_data):
    """
    Generate binary standstill flags based on gyroscope activity.
    1 = standstill, 0 = motion.
    """
    standstill = np.zeros(len(imu_data))
    counter_after_motion = 60
    cooldown = 60

    for i, m in enumerate(imu_data):
        if np.linalg.norm(m[3:6]) < 0.13:  # gyroscope quiet
            counter_after_motion += 1
            if counter_after_motion > cooldown:
                standstill[i] = 1
        else:
            standstill[i] = 0
            standstill[i - cooldown:i] = 0
            counter_after_motion = 0

    return standstill


# === PLOTTING ===
def plot_accelerations_before_and_after(accs, accs_calibrated):
    """
    Plot acceleration magnitude before and after calibration.
    """
    times = np.arange(0, len(accs_calibrated)) * 0.01

    fig, ax = plt.subplots(figsize=(8, 4))
    ax.plot(times, np.linalg.norm(accs, axis=1), color='red', alpha=0.7, label="Uncalibrated norm")
    ax.plot(times, np.linalg.norm(accs_calibrated, axis=1), color='green', alpha=0.7,
            label=f"Calibrated norm $g_{{mean}}$ = {np.linalg.norm(accs_calibrated, axis=1).mean():.2f} m/s²")
    ax.axhline(9.81, color='blue', linestyle='--', alpha=0.5, label="Ideal norm $g_{ideal}$ = 9.81 m/s²")

    ax.grid(True)
    ax.set(
        xlabel="Time [s]",
        ylabel="Acceleration [m/s²]",
        ylim=[9.81 - 1.5, 9.81 + 1.5],
        title="Accelerometer Calibration Results"
    )
    ax.legend()
    plt.tight_layout()
    #plt.savefig(FIG, dpi=500)
    plt.show()


# === MAIN EXECUTION ===
if __name__ == "__main__":
    standstill_flags = generate_standstill_flags(imu_data)
    accs = accs[standstill_flags > 0]
    accs_calibrated = calibrate_accelerometer(accs, acc_params)
    plot_accelerations_before_and_after(accs, accs_calibrated)

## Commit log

2025-10-24 new data with 2s stillstand
    [data.csv]
2025-10-24 integrated serial communication between pc and esp32
2025-10-24 Replaced imu-calib submodule with forked version
2025-10-24 trimmed resiual down to 75
    [data.csv]
2025-10-25 nochmal motorkunde machen mit dir und step usw in einer extra datei
2025-11-03 new esp32 file with platformio working
2025-11-10 Update calibration logic / bug fixes
    [data.csv, imu_accel_data.csv, imu_gyro_data.csv]
